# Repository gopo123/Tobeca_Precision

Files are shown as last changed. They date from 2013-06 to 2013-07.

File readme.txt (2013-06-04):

Vous êtes sur le github de la version Précision de la Tobeca.
Les fichiers communs à la Tobeca et la Tobeca Précision ne sont pas copiés ici, il faut les récupérer directement depuis le dépôt de la Tobeca : https://github.com/pyroboynroses/Tobeca

Seuls les fichiers qui diffèrent ou qui sont nouveaux sont présents ici.

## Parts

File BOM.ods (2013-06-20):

Produit | Qte | Notes | Lien
Pièces imprimées PLA | 1 | PLA Faberdashery
CHARIOT_Y | 1
CLIP_ENDSTOP_Y | 1
CLIP_PLATEAU | 2
COIN | 8
COUPLAGE_Z X4 | 1
ETIQUETTE | 1
EXTRUDEUR | 1
EXTRUDEUR_SUPPORT_608ZZ | 1
FIX_CHARIOT_X | 2
JOUE_608ZZ | 1
MOLETTE | 6
PLAQUE_ARRIERE | 1
RETOUR_Y | 1
SANGUINOLOLU_CASE | 1
SUPPORT_RANGEMENT | 2
SUPPORT_BOBINE | 1
SANGUINOLOLU_TOP | 1
FIX_ARBRE_Z | 4
PLAQUE_MOTEUR_X | 1
PLAQUE_RETOUR_X | 1
PRESSE_DOUILLE_X | 4
SUPPORT_608ZZ_TOP | 2
SUPPORT_AXE_X | 2
SUPPORT_ENDSTOP_Z | 1
SUPPORT_AXE_Y | 4
SUPPORT_FAN_X | 1
Electricité et électronique
Kit Sanguinololu | 1 | Avec endstops
Stepper Driver A4988 | 4
Alimentation 12V 120W | 1 |  | http://www.aliexpress.com/item/120W-12V-Ultra-thin-Single-Output-Switching-power-supply-for-LED-Strip-light/628890138.html
Thermistance 100K | 1 | pour plateau chauffant
Ampoule LED précablée | 1
Moteur NEMA14 | 2
Moteur NEMA17 | 3
Hot end | 1 |  | http://cgi.ebay.fr/2x-HotEnd-Fully-Assembled-and-Wired-FREE-Hobbed-Bolt-RepRap-3D-Printer-Hot-End-/281040096095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
Cordon secteur IEC mâle 2m | 1 |  | http://www.conrad.fr/ce/fr/product/060465/Cordons-secteur-1016-A-250-V-AC
Interrupteur à bascule | 2 |  | http://www.conrad.fr/ce/fr/product/700847/Interrupteur-bascule-noir-OnOff-250-VAC-6-A-sans-clairage-SCI-R13-66A-02
Embase IEC mâle snap-in | 1 |  | http://www.conrad.fr/ce/fr/product/501626/Embase-secteur-mle-IEC-noire-Snap-in-avec-porte-fusible-Kaiser-B85313AB3
Fusible 1A 5x20mm | 2 | dont un de secours | http://www.conrad.fr/ce/fr/product/533491/10-Fus-5X20Mm-1A-Retarde-ESKA-522517-1A;jsessionid=626176F761C74083CEBC79497046A828.ASTPCEN27
Ventilateur Akasa Led 40mm | 3 |  | http://www.conrad.fr/ce/fr/product/998689/Ventilateur-4-cm-AKASA-bleu
gaîne thermo 2mm (au mètre) | 1
Cable USB A to B 3m | 1 |  | http://www.conrad.fr/ce/fr/product/990684/Cble-USB-20-CONRAD-AB-3m-Bulk
Résistance de puissance 3,3ohms 10W | 6 |  | http://it.mouser.com/Search/ProductDetail.aspx
Câblage (au mètre)
Cablewrap 12mm | 2
Colliers nylon 160mm | 20
Colliers nylon 100mm | 20
Câble RJ45 | 2 | 2 fils x 1150mm (LED) 2 fils x 500mm (T plateau) 2 fils x 1000mm (T extrudeur) 2 fils x 750mm (endstop X) 2 fils x 515mm (endstop Y) 2 fils x 400mm (endstop Z) 4 fils x 800mm (moteur extrudeur) 4 fils x 300mm (moteur X)
Câble double 0,75mm² | 2,5 | 1x350mm (alimentation carte) 1x500mm (raccordement R plateau) 1x1000mm (R extrudeur) 1x400mm (interco R plateau)
Câble triple 0,75mm² | 0,1 | 1x70mm (alimentation 220V)
Mécanique
HTD3 aluminium pulley | 2 |  | http://www.beltingonline.com/14-tooth-t5-pulley-al21t5-4896
Plaque alu 3mm 210x210mm | 1
Plaque alu 3mm 73x70mm | 1
Bouleau 9mm 210x210mm | 1 | support plateau
Plaque verre 4mm 210x210mm | 1
Douille Igus RJM-01 8mm | 8
Accouplement flexible 5x8mm | 2
Arbre alu 8mm 420mm | 6
Arbre alu 8mm 301mm | 2
HTD3 belt 840mm | 1
HTD3 belt 680mm | 1
608ZZ ball bearing | 3
Ressorts | 5 | plateau, extrudeur
M4 brass insert | 1
Visserie | 1
Vis M3x6mm | 4
Vis M3x8mm | 4
Vis M3x10mm | 5
Vis M3x20mm | 50
Vis M3x25mm | 8
Vis M3x30mm | 4
Vis M3x40mm | 20
Vis M3x60mm | 8
Vis M3x16mm tête fraisée | 24
Vis M3x20mm tête fraisée | 8
Vis M3x40mm tête fraisée | 4
Rondelles M3 larges | 60
Rondelles M3 standards | 87
Ecroux nylstop M3 | 22
Ecroux M3 | 127
Ecrous M8 | 2
Vis M8x25mm | 2
Ecrous long M8 | 2
Tige filetée M8 inox A2 roulée 365mm | 2 | 2x345mm (axe Z)
Tige filetée M8 inox A2 roulée 25mm | 1 | extrudeur
Rivets Pop 4x25mm | 50
Tube alu 12mm 415mm | 4 | 4x410mm (axe Z)
Divers, usage ponctuel
Pâte thermique | 1 | pour résistances plateau chauffant
Mallette |  | #REF !
Bouleau 9mm 443x414mm | 2
Bouleau 9mm 443x94mm | 2 | châssis
Bouleau 9mm 414x94mm | 2 | châssis
Bouleau 9mm 443x80mm | 2 | capot
Bouleau 9mm 414x80mm | 2 | capot
Fermeture grenouille cadenassable | 4
Mousse 5mm plastazote 390x425mm | 1 | adhésive pour l'intérieur du capot | http://casetor-flight-case.com/boutique/product_info.php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
Poignée à sangle | 1

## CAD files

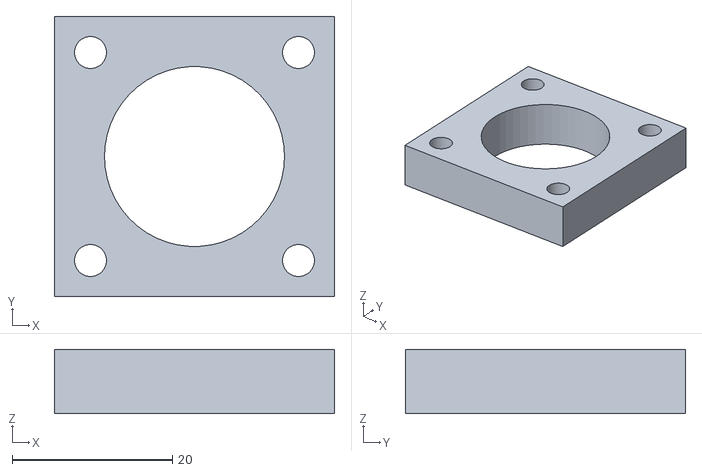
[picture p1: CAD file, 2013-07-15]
STL/SUPPORT_608ZZ_TOP.stl
35.0 x 35.0 x 8.00

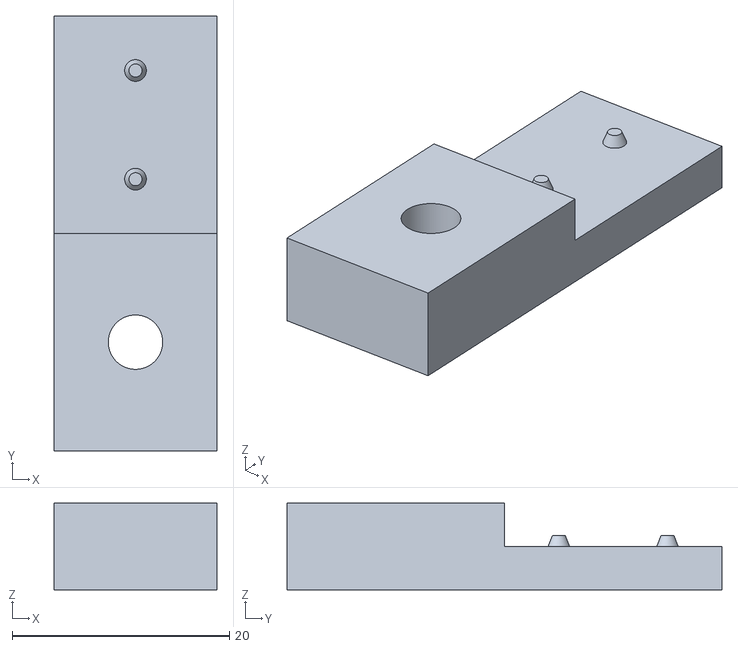
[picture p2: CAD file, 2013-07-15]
STL/SUPPORT_ENDSTOP_Z.stl
15.0 x 40.0 x 8.00

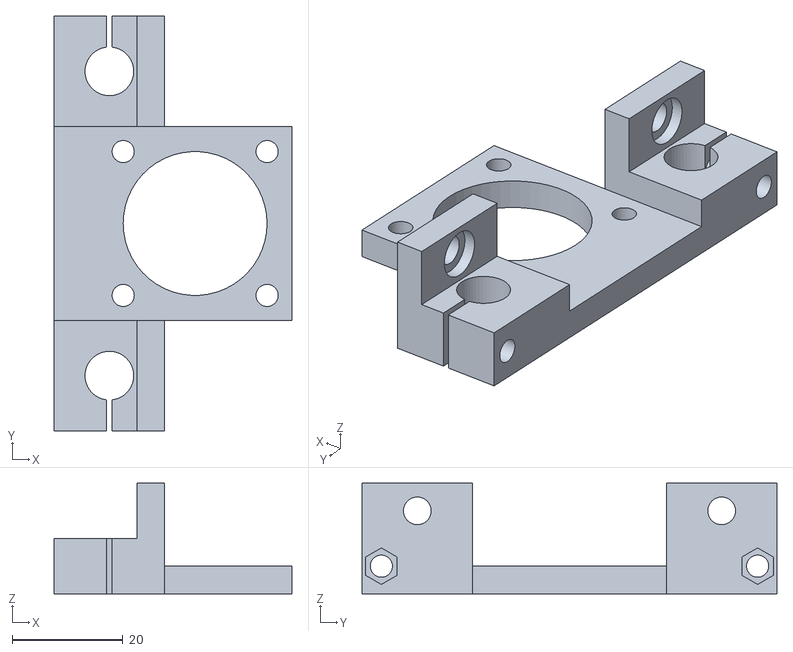
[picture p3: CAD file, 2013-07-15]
STL/FIX_MOTEUR_Z.stl
43.0 x 75.0 x 20.0

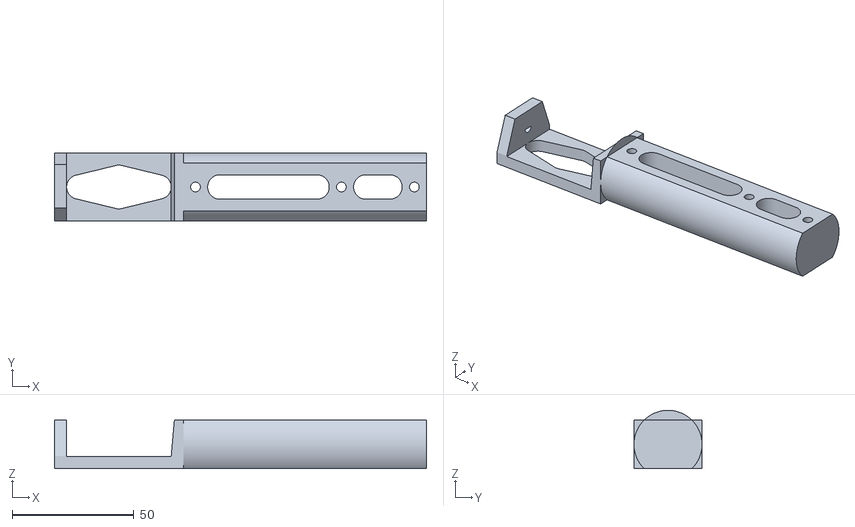
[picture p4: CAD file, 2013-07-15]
STL/SUPPORT_BOBINE.stl
153.0 x 28.0 x 24.0

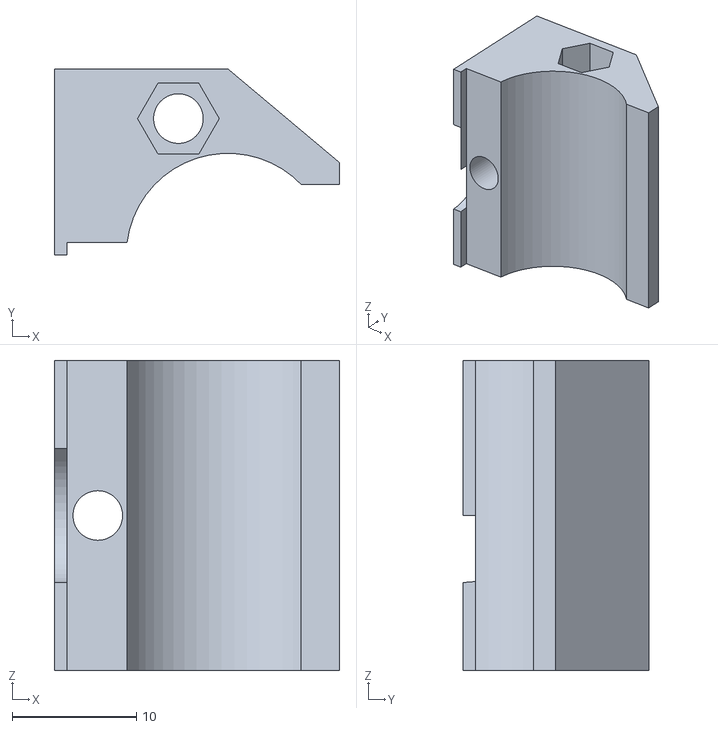
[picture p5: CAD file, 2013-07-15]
STL/PRESSE_DOUILLE_X.stl
23.0 x 15.0 x 25.0

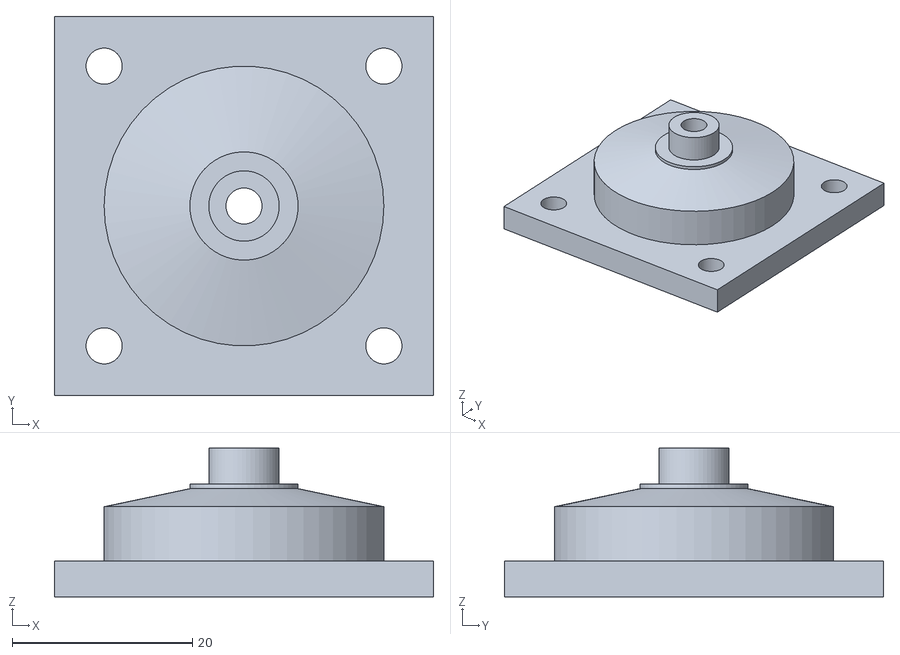
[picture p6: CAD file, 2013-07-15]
STL/RETOUR_X.stl
42.0 x 42.0 x 16.5

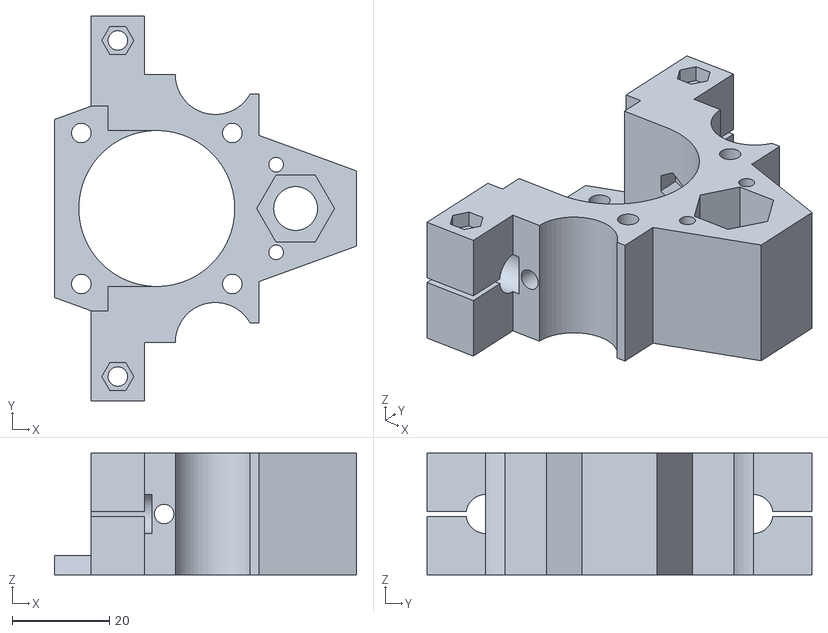
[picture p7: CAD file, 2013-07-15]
STL/SUPPORT_AXE_X.stl
62.0 x 79.0 x 25.0

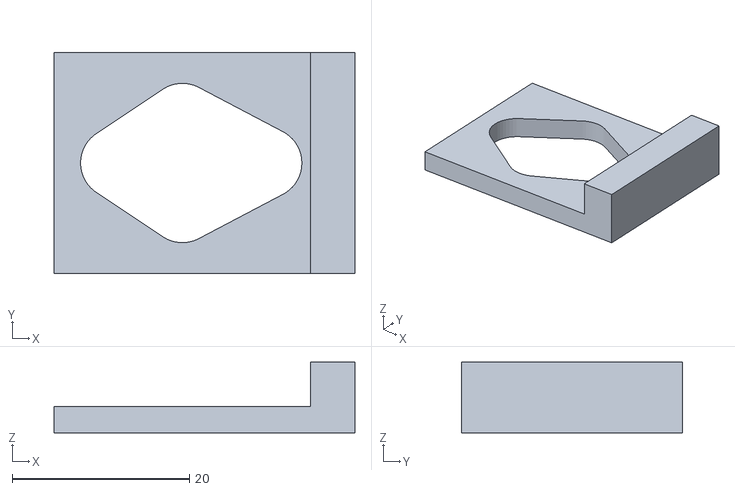
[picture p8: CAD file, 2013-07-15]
STL/SUPPORT_RANGEMENT.stl
34.0 x 25.0 x 8.00

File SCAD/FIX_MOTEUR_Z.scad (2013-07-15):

r_arbre=4.4;
r_m3=2;
r_ecrou_m3=3.3;
r_m4=2.5;
r_tete_m4=4;

module plaque_moteur(){
	difference(){
		cube([43,35,5]);
		translate([12.5,4.5,-2]){cylinder(r=r_m3, h=10, $fn=50);}
		translate([38.5,4.5,-2]){cylinder(r=r_m3, h=10, $fn=50);}
		translate([12.5,30.5,-2]){cylinder(r=r_m3, h=10, $fn=50);}
		translate([38.5,30.5,-2]){cylinder(r=r_m3, h=10, $fn=50);}
		translate([25.5,17.5,-2]){cylinder(r=13, h=10, $fn=50);}
	}
}
module fix_arbre(){
	difference(){
		cube([20,20,20]);
		translate([0,0,10]){cube([15,20,15]);}
		translate([10,10,15]){rotate([0,90,0])cylinder(r=r_m4, h=20, $fn=50);}
		translate([10,10,15]){rotate([0,90,0])cylinder(r=r_tete_m4, h=7, $fn=50);}
		translate([10,10,-5]){cylinder(r=r_arbre, h=20, $fn=50);}
		translate([-5,3.5,5]){rotate([0,90,0])cylinder(r=r_m3, h=50, $fn=50);}
		translate([15,3.5,5]){rotate([0,90,0])cylinder(r=r_ecrou_m3, h=20, $fn=6);}
		translate([9.5,-5,-5]){cube([1,15,20]);}
	}
}
plaque_moteur();
translate([0,-20,0]){fix_arbre();}
translate([0,55,0]){mirror([0,1,0]){fix_arbre();}}

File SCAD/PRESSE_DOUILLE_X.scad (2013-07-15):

r_douille=8.2;
r_m3=2;
r_ecrou_m3=3.3;
r_arbre=4.4;
height=25;

module presse_douille(){
	difference(){
		cube([23,15,height]);
		
		//passage douille
		translate([14,0,-5]){cylinder(r=r_douille, h=height+10, $fn=50);}

		//extrusions principales
		translate([14,-2,-5]){cube([15,7.7,height+10]);}
		translate([1,-2,-5]){cube([15,3,height+10]);}
		translate([14,15,-5]){rotate([0,0,-40])cube([15,15,height+10]);}

		//trou pour réglage endstop Z
		translate([10,11,-5]){cylinder(r=r_m3, h=height+10, $fn=50);}
		translate([10,11,height-5]){cylinder(r=r_ecrou_m3, h=height, $fn=6);}

		//extrusion pour passage de fin de l'arbre
		translate([-height,0,height/2]){rotate([0,90,0])cylinder(r=r_arbre+1, h=height+1, $fn=50);}

		//trou latéral pour vissage
		translate([3.5,0,height/2]){rotate([0,90,90])cylinder(r=r_m3, h=height, $fn=50);}

	}
}
presse_douille();

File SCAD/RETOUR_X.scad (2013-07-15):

r_m3=2;
r_ecrou_m3=3.3;
r_m8=3.9;
ep_608=8;
ep=4;
l=42;
height=25;

module retour_x(){
	difference(){
		union(){
		cube([l,l,ep]);

		//flasque roulement
		translate([l/2,l/2,ep]){cylinder(r=15.5, h=height/2-2-ep_608/2-0.5, $fn=50);}
		translate([l/2,l/2,ep+height/2-2-ep_608/2-0.5]){cylinder(r1=15.5, r2=6, h=2, $fn=50);}
		translate([l/2,l/2,ep+height/2-2-ep_608/2+2-0.5]){cylinder(r=6, h=0.5, $fn=50);}
		translate([l/2,l/2,ep+height/2-2-ep_608/2+2]){cylinder(r=r_m8, h=ep_608/2, $fn=50);}
		}
	
		//trous pour fixation
		translate([5.5,5.5,-5]){cylinder(r=r_m3, h=15, $fn=50);}
		translate([l-5.5,5.5,-5]){cylinder(r=r_m3, h=15, $fn=50);}
		translate([5.5,l-5.5,-5]){cylinder(r=r_m3, h=15, $fn=50);}
		translate([l-5.5,l-5.5,-5]){cylinder(r=r_m3, h=15, $fn=50);}
		
		translate([l/2,l/2,-5]){cylinder(r=r_m3, h=50, $fn=50);}

		
	}


}
retour_x();

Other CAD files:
SCAD/SUPPORT_608ZZ_TOP.scad
SCAD/SUPPORT_AXE_X.scad
SCAD/SUPPORT_BOBINE.scad
SCAD/SUPPORT_ENDSTOP_Z.scad
SCAD/SUPPORT_RANGEMENT.scad
SKP/COMPLET.skp
SKP/PORTIQUE.skp

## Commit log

2013-05-12 Premier commit
    [BOM.ods]
2013-05-14 Première ébauche du portique
    [BOM.ods, PORTIQUE.skp, Tobeca Précision.skp]
2013-05-14 Ajout des supports de moteurs et d'axes Z
    [PORTIQUE.skp, Tobeca Précision.skp]
2013-06-16 Optimisation SUPPORT_AXE_X
    Suite idées proposées par Stéphane
    [COMPLET.skp, PORTIQUE.skp]
2013-06-16 Finalisations pièces principales
    [PORTIQUE.skp]
2013-06-16 Tobeca Precision complète
    [COMPLET.skp]
2013-06-17 MàJ des fichiers + support endstop Z
    [PORTIQUE.skp]
2013-06-17 Modification serrage douilles Z
    Suite proposition de Stéphane Bastian sur le forum :
    http://www.reprap-diffusion.fr/forums/topic/14-5mm-a-recuperer/page/2/#post-2121
    [PORTIQUE.skp]
2013-06-20 Fichiers STL
    Ajout des fichiers STL non corrigés + support bobine + perçages flancs
    alu
    [BOM.ods, COMPLET.skp, FIX_ARBRES_Z.stl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]
2013-07-15 Pièces fonctionnelles
    Testées sur le prototype TP-001
    [Configuration.h, Configuration_adv.h, FIX_ARBRES_Z.stl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]
